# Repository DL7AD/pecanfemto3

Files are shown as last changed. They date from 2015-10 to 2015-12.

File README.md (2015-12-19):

# Pecan Femto 3

This is a small APRS tracker which has been made especially for balloon tracking. When designing this PCB we took into account to get a small PCB with basic tracking functions with less features. This PCB has been designed after we build Pecan Pico 6 and we did some changes compared to the last one.

- We took a NXP LPC824 microcontroller insteas of the LPC1114. It has a pin switch matrix, which basically means that almost every pin can be taken for every function.
- We took a much smaller TCXO.
- We left the parts for TCXO modulation.
- The uBlox MAX7C has been replaced by an uBlox EVA7M module which is basically a smaller and lighter GPS receiver.
- Added a Step-Down regulator in the power management in order to make the use of LiPO's available.
- We removed the ability to receive for this tracker.
- The GPS is switched by the microcontroller.

Like the Pecan Pico 6, this PCB is also solar enabled. So the tracker could stay almost alive forever.

Versions
========
- Pecan Femto 3a can be found in [branch master](https://github.com/DL7AD/pecanfemto3/tree/master) !!! CONTAINS ERRORS
- Pecan Femto 3b can be found in [branch 3b](https://github.com/DL7AD/pecanfemto3/tree/3b)

PCB errors
==========
At version 3a, we've done some errors on the PCB:

- The TCXO pins are flipped
- There's an pullup resistor missing at RADIO_SDN (because it's connected to a pin a the microcontroller, which has no internal pullup capability)

Version 3b sould actually have no errors but we've never tested it.

Disadvantages and concept errors
================================

Since we use a different microcontroller, we did not take into account, that there's a different ISP entry pin for the LPC824. The ISP entry pin is located at pin PIO0_12 which we've used as GPS power pin. The problem is, that the tracker doesn't startup automatically, because the GPS power pin is held low by the GPS itself, so the microcontroller starts in ISP mode. There's only one solution for it: Enabling the CRP3 mode. Enabling CRP3 disables the ISP entry pin but it also lockes you out and you are not able to flash the chip anymore.

The PCB ro software also has a bug. Once the PCB is cooled down to -10°C, the modulation somehow changes and so far I couldn't find out, what the error is. The software for this Tracker can be found [here](https://github.com/DL7AD/pecan-lpc82x)

Software
========

Software can be found here: [pecan-lpc82x](https://github.com/DL7AD/pecan-lpc82x)

License
=======
CC-BY-SA 4.0

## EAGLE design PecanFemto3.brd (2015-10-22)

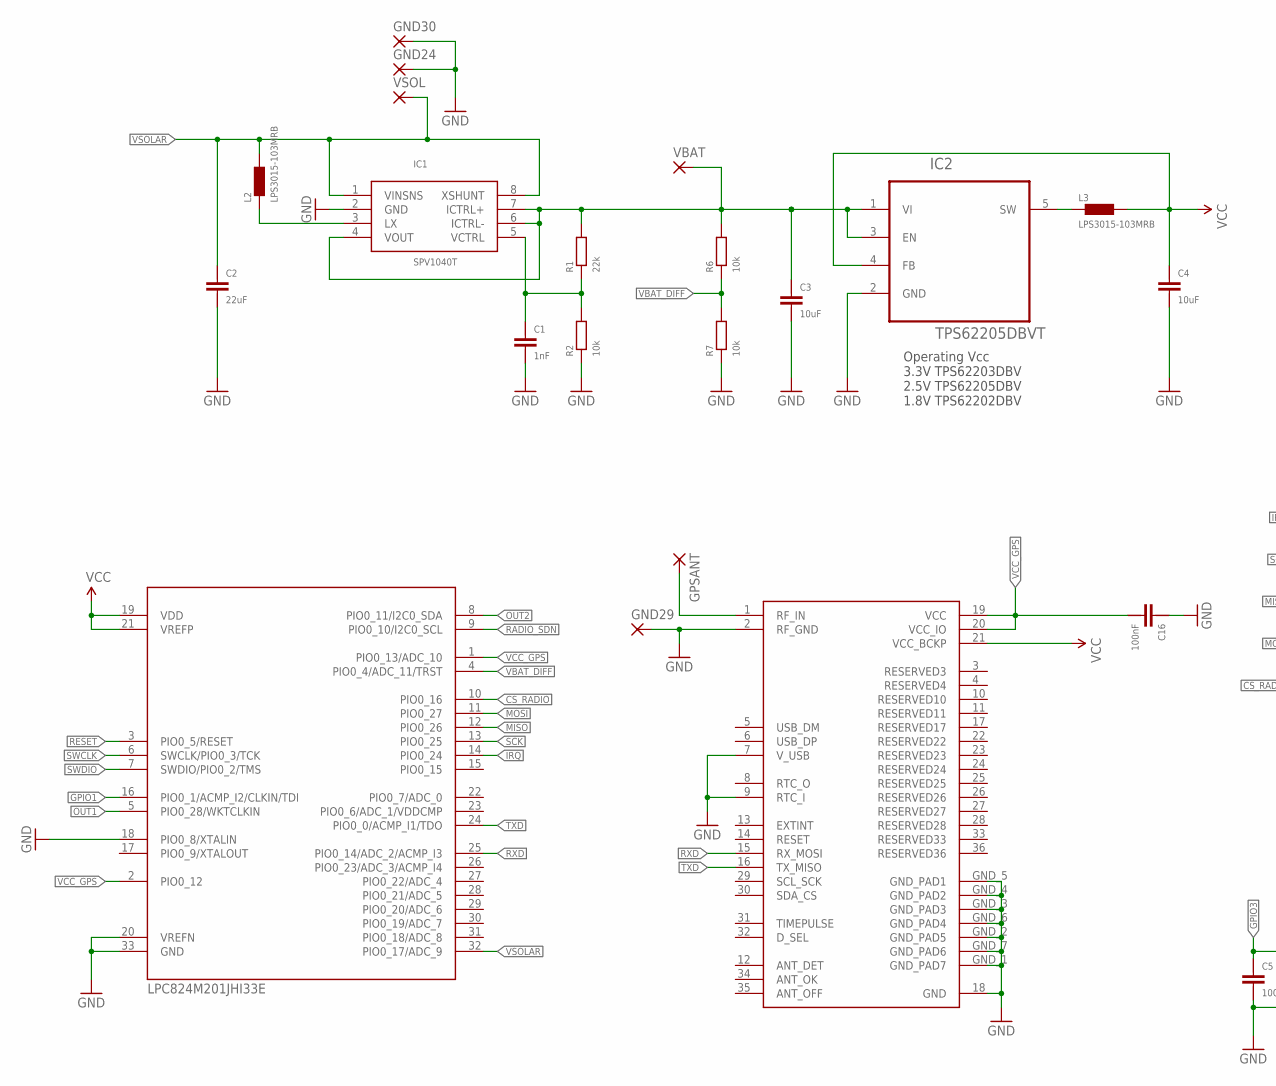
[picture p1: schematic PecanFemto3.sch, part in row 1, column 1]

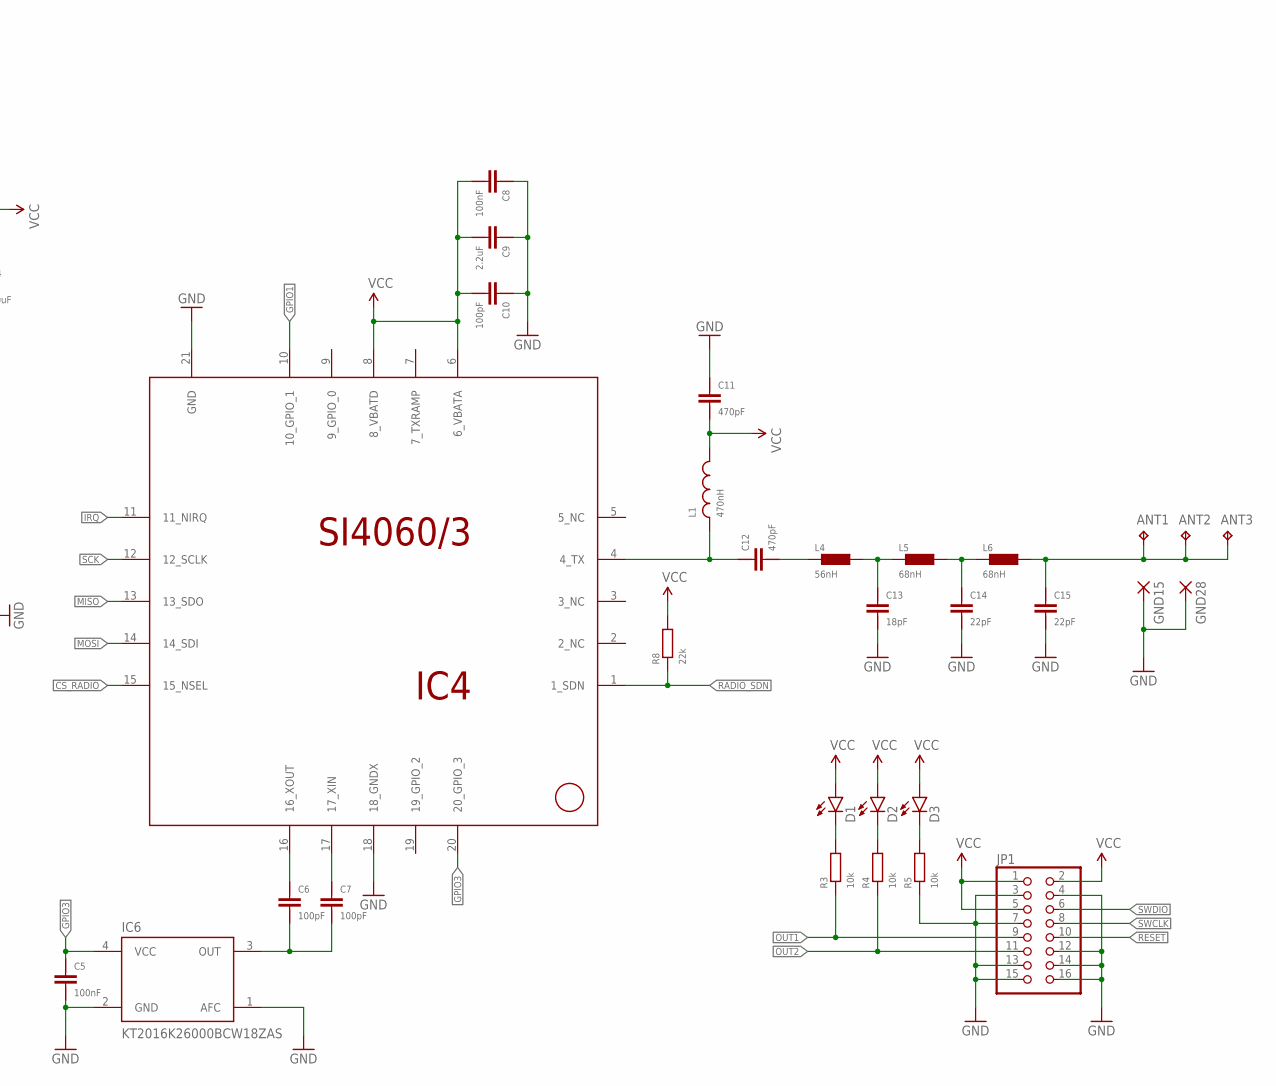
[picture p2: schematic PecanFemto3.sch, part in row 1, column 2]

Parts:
ANT1, ANT2, ANT3: TP; P1-7; MPN ERJ-3EKF62R0V
C1: 1nF; 0402
C2: 22uF; 0805
C3, C4: 10uF; 0805
C5, C8, C16: 100nF; 0402
C6, C7, C10: 100pF; 0402
C9: 2.2uF; 0402
C11, C12: 470pF; 0402
C13: 18pF; 0402
C14, C15: 22pF; 0402
D1, D2, D3: LED0603; LED-0603
GND15, GND24, GND28, GND29, GND30: SMD2; SMD1,27-2,54
GPSANT: SMD2; SMD1,27-2,54
IC1: SPV1040T; TSSOP8
IC2: TPS62205DBVT; SOT95P280X145-5N
IC3: EVA7M
IC4: SI4060/3; QFN-20
IC5: LPC824M201JHI33E; QFN65P500X500X100-33N
IC6: KT2016K26000BCW18ZAS; TCXO_2.0X1.6
JP1: PINHD-2X8; 2X08
L1: 470nH; 0805
L2, L3: LPS3015-103MRB; LPS3015
L4: 56nH; 0402
L5, L6: 68nH; 0402
R1, R8: 22k; 0402
R2, R3, R4, R5, R6, R7: 10k; 0402
VBAT: SMD2; SMD1,27-2,54
VSOL: SMD2; SMD1,27-2,54

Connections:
C12: C12.P$1 (1), L4.P$1 (1)
CS_RADIO: IC4.15 (15_NSEL), IC5.10 (PIO0_16)
GND: C1.P$1 (1), C2.P$1 (1), C3.P$1 (1), C4.P$1 (1), C5.P$1 (1), C8.P$2 (2), C9.P$2 (2), C10.P$2 (2), C11.P$2 (2), C13.P$1 (1), C14.P$1 (1), C15.P$1 (1), C16.P$2 (2), GND15.1, GND24.1, GND28.1, GND29.1, GND30.1, IC1.2 (GND), IC2.2 (GND), IC3.2 (RF_GND), IC3.7 (V_USB), IC3.9 (RTC_I), IC3.18 (GND), IC3.GND_1 (GND_PAD7), IC3.GND_2 (GND_PAD5), IC3.GND_3 (GND_PAD3), IC3.GND_4 (GND_PAD2), IC3.GND_5 (GND_PAD1), IC3.GND_6 (GND_PAD4), IC3.GND_7 (GND_PAD6), IC4.18 (18_GNDX), IC4.21 (GND), IC5.18 (PIO0_8/XTALIN), IC5.20 (VREFN), IC5.33 (GND), IC6.1 (AFC), IC6.2 (GND), JP1.3, JP1.4, JP1.7, JP1.12, JP1.13, JP1.14, JP1.15, JP1.16, R2.P$1 (1), R5.P$1 (1), R7.P$1 (1)
GPIO1: IC4.10 (10_GPIO_1), IC5.16 (PIO0_1/ACMP_I2/CLKIN/TDI)
GPIO3: C5.P$2 (2), IC4.20 (20_GPIO_3), IC6.4 (VCC)
IRQ: IC4.11 (11_NIRQ), IC5.14 (PIO0_24)
L5: C13.P$2 (2), L4.P$2 (2), L5.P$1 (1)
MISO: IC4.13 (13_SDO), IC5.12 (PIO0_26)
MOSI: IC4.14 (14_SDI), IC5.11 (PIO0_27)
unnamed: GPSANT.1, IC3.1 (RF_IN)
unnamed: C12.P$2 (2), IC4.4 (4_TX), L1.1
unnamed: ANT1.TP, ANT2.TP, ANT3.TP, C15.P$2 (2), L6.P$2 (2)
unnamed: C14.P$2 (2), L5.P$2 (2), L6.P$1 (1)
unnamed: C7.P$2 (2), IC4.17 (17_XIN)
unnamed: D1.C, R3.P$2 (2)
unnamed: C6.P$1 (1), C7.P$1 (1), IC6.3 (OUT)
unnamed: C6.P$2 (2), IC4.16 (16_XOUT)
unnamed: D2.C, R4.P$2 (2)
unnamed: D3.C, R5.P$2 (2)
unnamed: IC1.3 (LX), L2.1_1 (1), L2.1_2 (1), L2.1_3 (1), L2.1_4 (1), L2.1_5 (1), L2.1_6 (1), L2.1_7 (1), L2.1_8 (1), L2.1_9 (1)
unnamed: IC2.5 (SW), L3.1_1 (1), L3.1_2 (1), L3.1_3 (1), L3.1_4 (1), L3.1_5 (1), L3.1_6 (1), L3.1_7 (1), L3.1_8 (1), L3.1_9 (1)
unnamed: C1.P$2 (2), IC1.5 (VCTRL), R1.P$1 (1), R2.P$2 (2)
OUT1: IC5.5 (PIO0_28/WKTCLKIN), JP1.9, R3.P$1 (1)
OUT2: IC5.8 (PIO0_11/I2C0_SDA), JP1.11, R4.P$1 (1)
RADIO_SDN: IC4.1 (1_SDN), IC5.9 (PIO0_10/I2C0_SCL), R8.P$1 (1)
RESET: IC5.3 (PIO0_5/RESET), JP1.10
RXD: IC3.15 (RX_MOSI), IC5.25 (PIO0_14/ADC_2/ACMP_I3)
SCK: IC4.12 (12_SCLK), IC5.13 (PIO0_25)
SWCLK: IC5.6 (SWCLK/PIO0_3/TCK), JP1.8
SWDIO: IC5.7 (SWDIO/PIO0_2/TMS), JP1.6
TXD: IC3.16 (TX_MISO), IC5.24 (PIO0_0/ACMP_I1/TDO)
VBAT: C3.P$2 (2), IC1.4 (VOUT), IC1.6 (ICTRL-), IC1.7 (ICTRL+), IC2.1 (VI), IC2.3 (EN), R1.P$2 (2), R6.P$2 (2), VBAT.1
VBAT_DIFF: IC5.4 (PIO0_4/ADC_11/TRST), R6.P$1 (1), R7.P$2 (2)
VCC: C4.P$2 (2), C8.P$1 (1), C9.P$1 (1), C10.P$1 (1), C11.P$1 (1), D1.A, D2.A, D3.A, IC2.4 (FB), IC3.21 (VCC_BCKP), IC4.6 (6_VBATA), IC4.8 (8_VBATD), IC5.19 (VDD), IC5.21 (VREFP), JP1.1, JP1.2, JP1.5, L1.2, L3.2_1 (2), L3.2_2 (2), L3.2_3 (2), L3.2_4 (2), L3.2_5 (2), L3.2_6 (2), L3.2_7 (2), L3.2_8 (2), L3.2_9 (2), R8.P$2 (2)
VCC_GPS: C16.P$1 (1), IC3.19 (VCC), IC3.20 (VCC_IO), IC5.1 (PIO0_13/ADC_10), IC5.2 (PIO0_12)
VSOLAR: C2.P$2 (2), IC1.1 (VINSNS), IC1.8 (XSHUNT), IC5.32 (PIO0_17/ADC_9), L2.2_1 (2), L2.2_2 (2), L2.2_3 (2), L2.2_4 (2), L2.2_5 (2), L2.2_6 (2), L2.2_7 (2), L2.2_8 (2), L2.2_9 (2), VSOL.1

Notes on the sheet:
Operating Vcc 3.3V TPS62203DBV 2.5V TPS62205DBV 1.8V TPS62202DBV

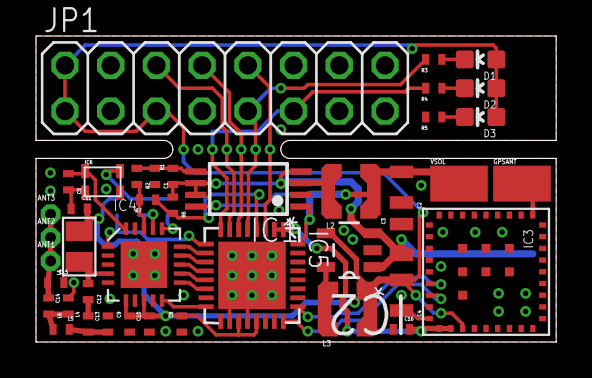
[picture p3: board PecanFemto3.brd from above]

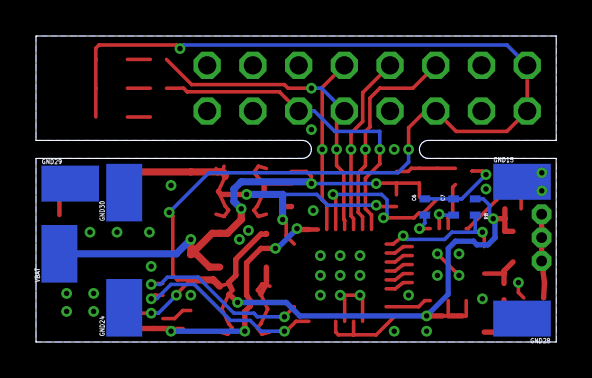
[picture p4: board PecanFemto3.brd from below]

Board: 2 copper layers, 28.9 x 17.0 mm, 51 parts (9 on the bottom side), 36 nets.

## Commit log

2015-07-21 Added step down converter
    [PecanFemto3.brd, PecanFemto3.sch]
2015-07-23 Moved components around
    [PecanFemto3.brd, PecanFemto3.sch]
2015-07-24 Moved parts around
    [PecanFemto3.brd, PecanFemto3.sch]
2015-07-27 Moved parts around, added MOSFET switch for GPS
    [PecanFemto3.brd, PecanFemto3.sch]
2015-08-05 Moved all parts around
    [PecanFemto3.brd, PecanFemto3.sch]
2015-08-11 Removed GPS-Switch-MOSFET and connected parts
    [PecanFemto3.brd, PecanFemto3.sch]
2015-08-11 Routed parts
    [PecanFemto3.brd, PecanFemto3.sch]
2015-08-13 Updated libraries, moved parts around, routed
    [PecanFemto3.brd, PecanFemto3.sch]
2015-08-13 Connected GND
    [PecanFemto3.brd]
2015-08-13 Moved parts, updated libs, added pads, added programmer pins
    [PecanFemto3.brd, PecanFemto3.sch]
2015-08-13 Added via
    [PecanFemto3.brd]
2015-08-13 Moved via
    [PecanFemto3.brd]
2015-08-26 Added LEDs, changed size of pinheader, moved parts
    [PecanFemto3.brd, PecanFemto3.sch]
2015-08-27 Connected TCXO VCC to Si4464
    [PecanFemto3.brd, PecanFemto3.sch]
2015-08-27 Connected V_USB and RTC_I to GND
    [PecanFemto3.brd, PecanFemto3.sch]
2015-08-29 Added Gerber files for hackvana
    [PecanFemto3-Vcut.gbr, PecanFemto3_board_outline.gm1, PecanFemto3_bottom_copper.gbl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]
2015-09-01 Moved parts around, updated GERBERs
    [PecanFemto3.brd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]
2015-09-03 Changed naming of parts
    [PecanFemto3.brd, PecanFemto3.sch]
2015-09-27 Moved parts in schematic, added PNG files
    [PecanFemto3.brd, PecanFemto3.sch]
2015-10-22 Changed part values
    [PecanFemto3.brd, PecanFemto3.sch]
2015-10-22 Fixed PecanPico3 errors Removed paste from large pads Added pullup to RADIO_SDN Fixed TCXO swapping (pins inverted) Updated Designators (on silkscreen layer)
    [PecanFemto3.brd, PecanFemto3.sch]
2015-10-22 Removed old gerber and picture exports
    [PecanFemto3-Vcut.gbr, PecanFemto3_board_outline.gm1, PecanFemto3_bottom_copper.gbl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]
2015-10-22 Changed TCXO designator, improved EVA7M package
    [PecanFemto3.brd, PecanFemto3.sch]

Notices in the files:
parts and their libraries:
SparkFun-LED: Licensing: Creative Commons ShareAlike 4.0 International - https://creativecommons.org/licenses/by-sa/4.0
